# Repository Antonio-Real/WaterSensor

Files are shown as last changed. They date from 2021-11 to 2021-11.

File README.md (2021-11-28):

# **WaterSensor project**
 Wireless sensor for monitoring the level of a remote water tank.

 The motivation for this small home project came from the need to monitor the water level of a water tank used for watering. When the tank empties it causes air to fill the pipes and hoses, making it a bit of a pain to get out. With this system its easier to know when the tank is about to empty and flip a switch to turn on a water pump (in the future this system will automatically control the pump).

 ## **System overview**

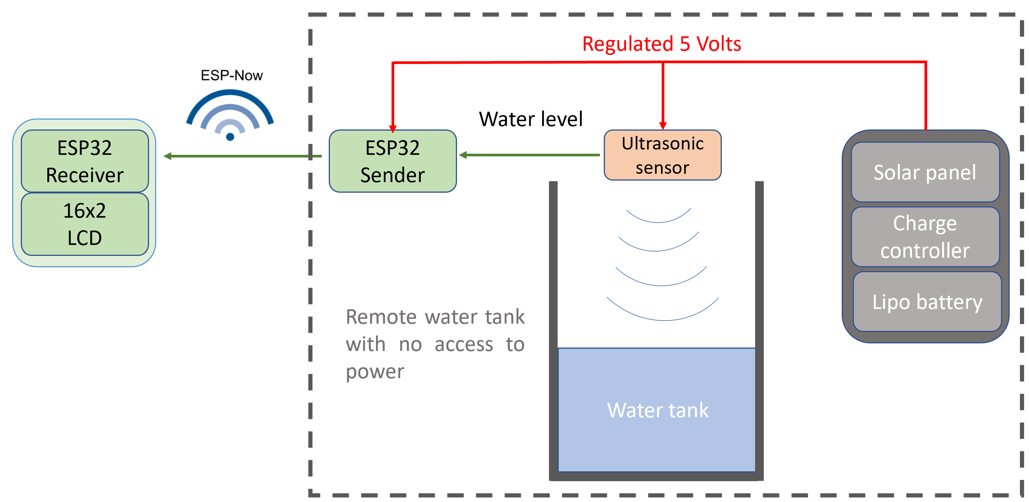
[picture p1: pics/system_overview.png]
system_overview
 

In simple terms, the water level is read by a HC-SR04 ultrasonic sensor which works well on water and doesn't corrode like those contact sensors you dip into water. The sensor data is acquired by a ESP32 and sent to a second ESP32 in another location using ESP-NOW which works well over longer distances and has smaller overhead than WIFI. The water level is then displayed on a standard 16x02 LCD.

One of the challenges of the system came from the fact that the water tank is in a place with no power, so a solar panel made sense to power the sensor and microcontroller. A charge controller and a Lipo battery work together with the solar panel to regulate power to a stable 5V and provide power in periods of no sun. The ESP32 sender board was custom designed to have minimal components to save battery.

## **Materials/tools used**

- 5W Solar panel and solar power management module bought from [Waveshare](https://www.waveshare.com/solar-power-manager.htm).
- 1800 mAh Lipo battery.
- Custom designed ESP32 board.
- HC-SR04 Ultrasonic sensor.
- A second generic ESP32 board + 16x02 LCD.
- Creality Ender 3v2 for printing the enclosures for the PCB, sensor and power module to protect from dust.

## **Repository contents**

| Folder/Files | Description |
| --- | --- |
| [pcb](/pcb) | Details and CAD files of the custom ESP32 board made for this project |
| [firmware](/firmware)  | Firmware of both the receiver and sender ESP32 boards |
| [models](/models) | STL files of the 3D printed parts for the enclosures |

## **Pictures**

parts_pic

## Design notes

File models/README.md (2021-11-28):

# **3D models in STL format**

Models that I fully designed in solidworks:
 - [Case](/models/custom_pcb_case) for custom PCB.

Models found in Thingiverse:
- [Clamp](/models/clamp) with gopro mounting system found [here](https://www.thingiverse.com/thing:4561329).
- [HC-SR04 case](/models/hcsr04_case) found [here](https://www.thingiverse.com/thing:3738687) but I adapted it with a gopro mount so it works with the clamp.
- [Solar charger case](/models/solar_charger_case) found [here](https://www.thingiverse.com/thing:4614783) with some changes to make it slightly larger to accomodate the battery.
- [LCD case](/models/lcd_case) found [here](https://www.thingiverse.com/thing:3839594).

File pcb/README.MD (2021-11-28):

# **Wireless sensor board**

This PCB design was kept to a minimum in order to optimize power consumption since it will function on a lipo battery. The main features:

- AP2112 3.3V low dropout (~50mV drop at 100mA) regulator to step down from the 5V that comes from the battery circuit.
- ESP32 microcontroller responsible for reading the HC-SR04 sensor and sending it through ESP-NOW protocol to a second ESP32.
- Screw terminals to easily connect the battery and the HC-SR04 ultrasonic sensor.

The PCB was designed using **Kicad 5.99** nightly build (soon to be released as Kicad 6).

 <br/><br/>

## **Schematic**
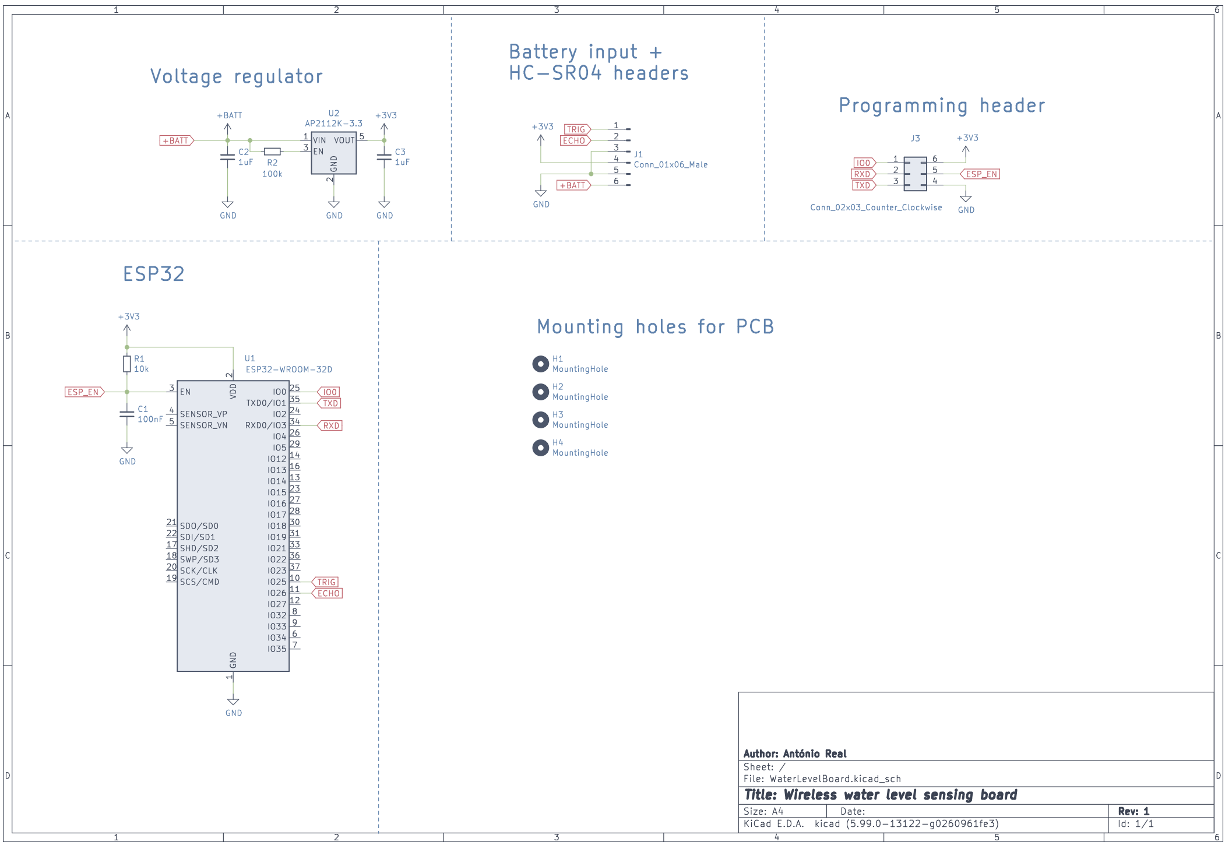
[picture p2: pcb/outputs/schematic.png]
pcb_sch


## **3D render of the PCB**
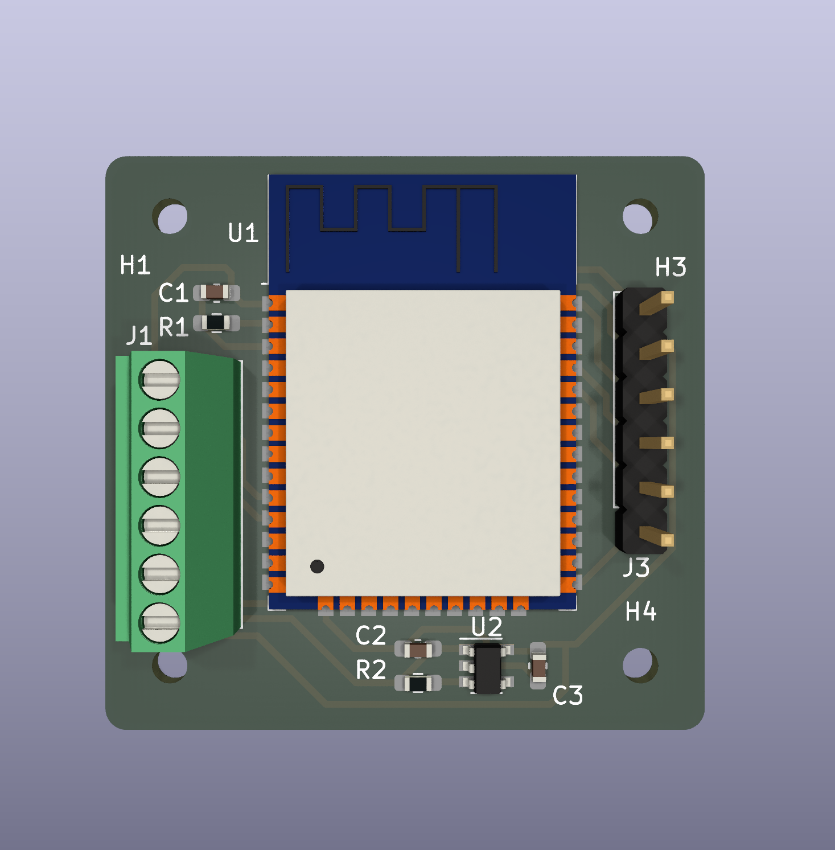
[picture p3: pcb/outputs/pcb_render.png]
pcb_render


## **Manufactured PCB**
The PCB was manufactured in a PCB milling machine and unfortunately came out poorly and required some enameled wire to replace the damaged tracks.
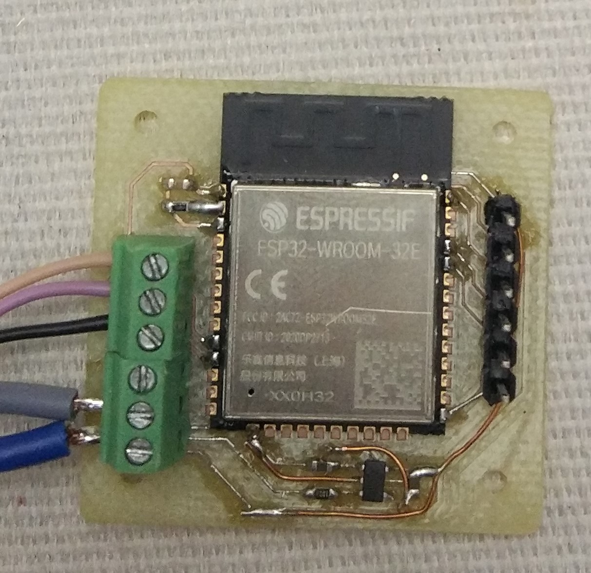
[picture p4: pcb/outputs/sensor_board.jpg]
pcb_manuf


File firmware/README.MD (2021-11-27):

# **Firmware of ESP32 water sensor sender/receiver**

The firmware was developed using VSCode with the PlatformIO extension and uses its build system and library management. Upon closer inspection of the `platformio.ini` file you can see two environments: `esp32_sender` and `esp32_receiver`. This was done to combine the firmwares of both boards in this repo since they're relatively simple.

By choosing one of the environments, the build system will automatically download the respective dependencies of each firmware and the respective main file (`main_sender.cpp` and `main_receiver.cpp`) found in `src` folder.

## **Common functionality**

In both boards Over-the-air (OTA) updates was included but we only want to run OTA when required. In a normal situation the boards will initialize ESP-NOW and communicate with each other but if GPIO 0 is pressed instead the boards initialize OTA and wait for the firmware to be uploaded.

## **Sensor sender**

This board is responsible for periodically taking a water level measurement with the HC-SR04 sensor and sending it to the receiver (receiver MAC address already known to the sender) using ESP-NOW  and then going back to sleep to maximize battery duration.

## **Sensor receiver**

This board is responsible for receiving the sensor readings and showing the values in percentage in a standard 16x02 LCD.

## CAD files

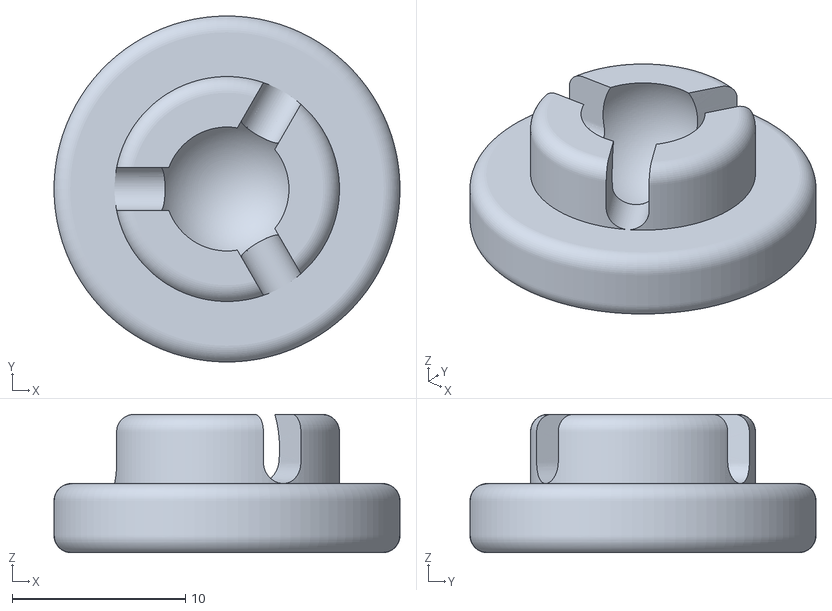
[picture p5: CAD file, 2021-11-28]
models/clamp/clamp_protector.stl
20.0 x 20.0 x 8.00

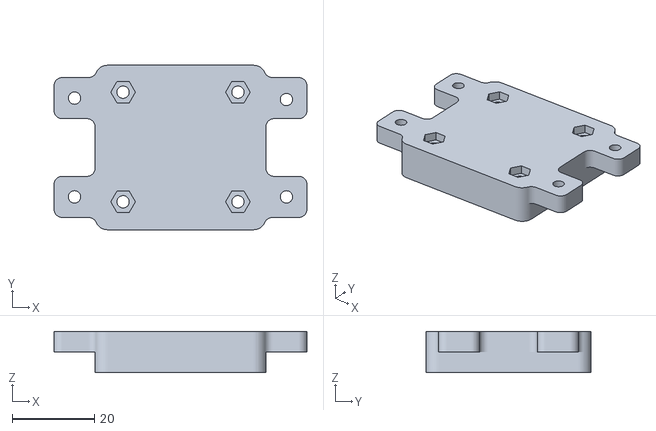
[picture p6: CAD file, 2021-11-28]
models/custom_pcb_case/pcb_case_bottom.STL
61.6 x 40.0 x 10.0

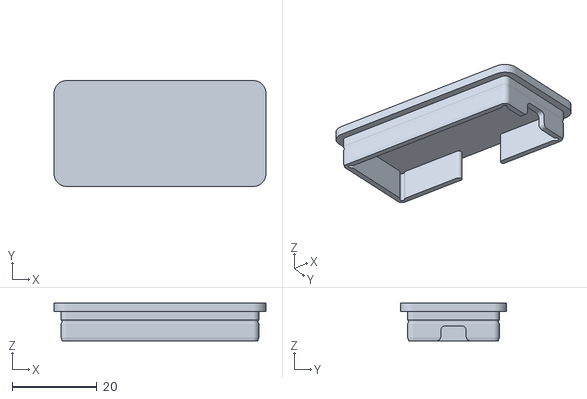
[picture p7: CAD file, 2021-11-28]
models/hcsr04_case/cover_hcsr04.STL
50.0 x 25.0 x 8.90

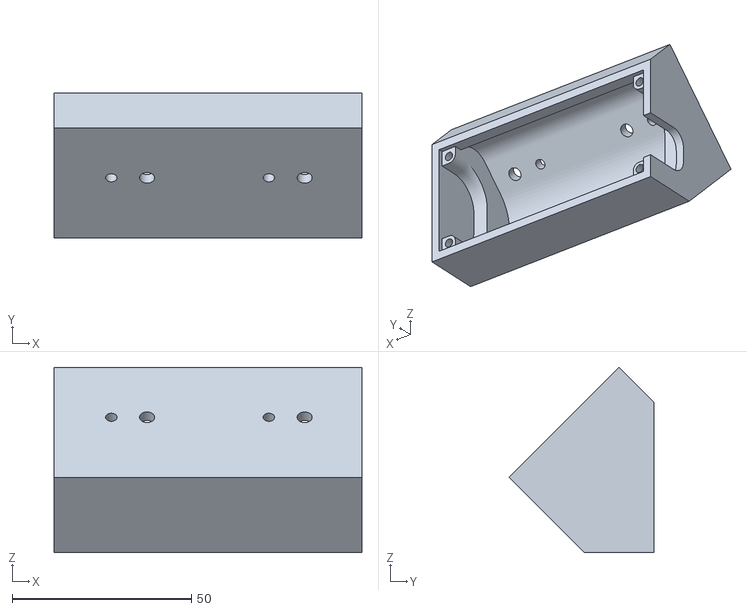
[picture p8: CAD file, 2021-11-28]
models/lcd_case/16x2_back_45deg_m3.stl
86.0 x 40.4 x 51.7

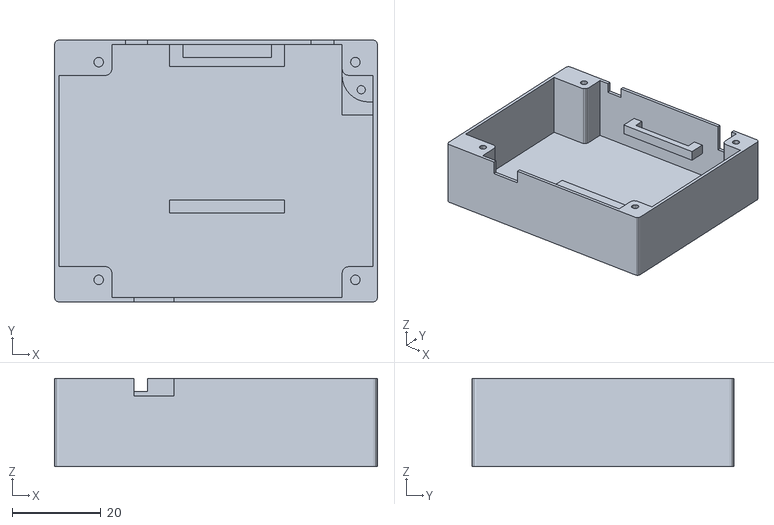
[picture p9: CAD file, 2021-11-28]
models/solar_charger_case/charger_case_top.STL
73.0 x 59.2 x 20.0

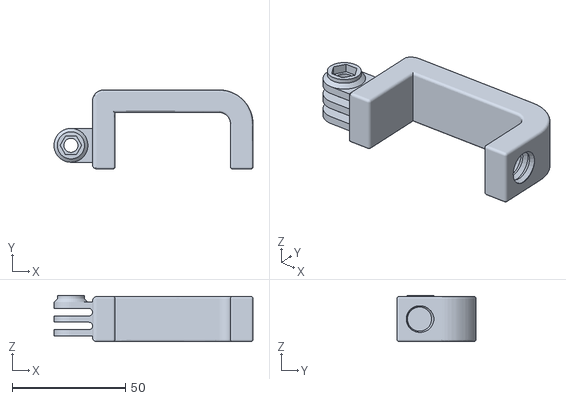
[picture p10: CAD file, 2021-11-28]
models/clamp/gopro_g-clamp.stl
88.0 x 35.0 x 20.5

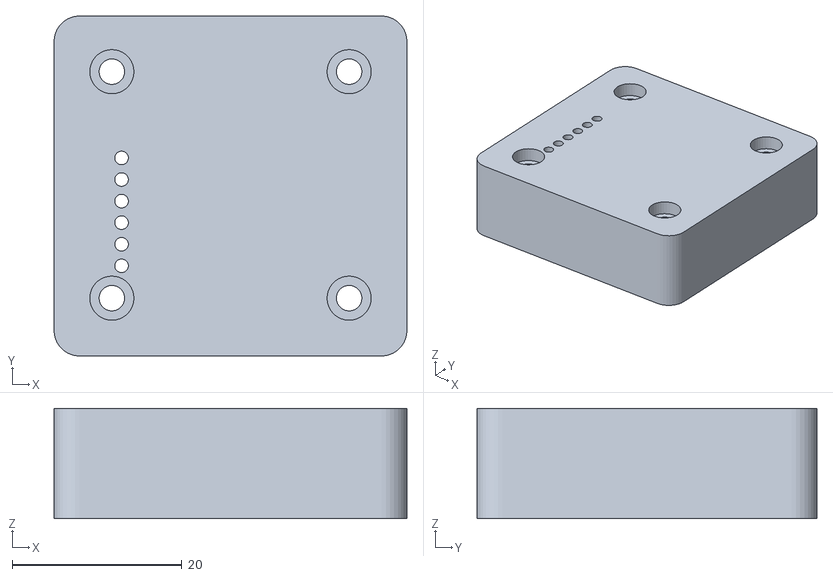
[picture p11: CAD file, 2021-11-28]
models/custom_pcb_case/pcb_case_top.STL
41.6 x 40.0 x 13.0

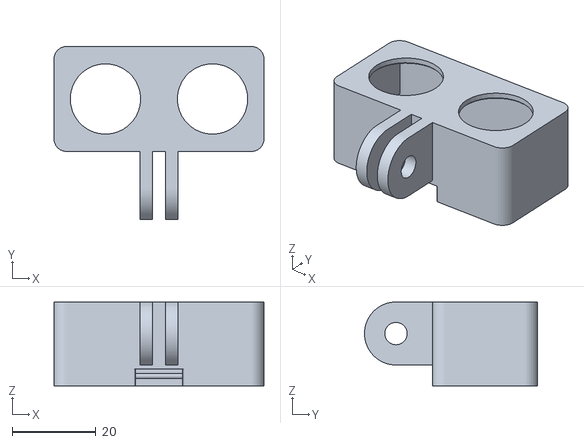
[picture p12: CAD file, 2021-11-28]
models/hcsr04_case/case_hcsr04.STL
50.0 x 41.2 x 20.0

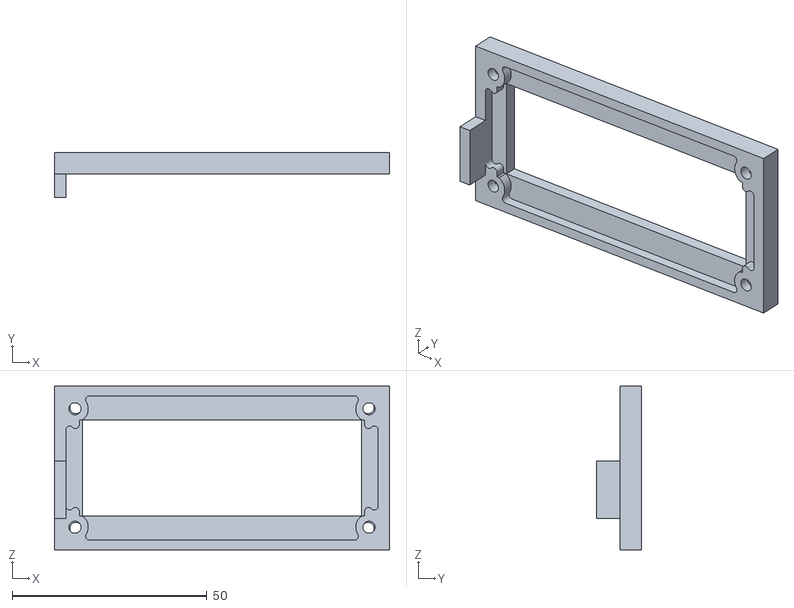
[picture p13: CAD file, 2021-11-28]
models/lcd_case/16x2_front_small_m3.stl
86.0 x 11.5 x 42.0

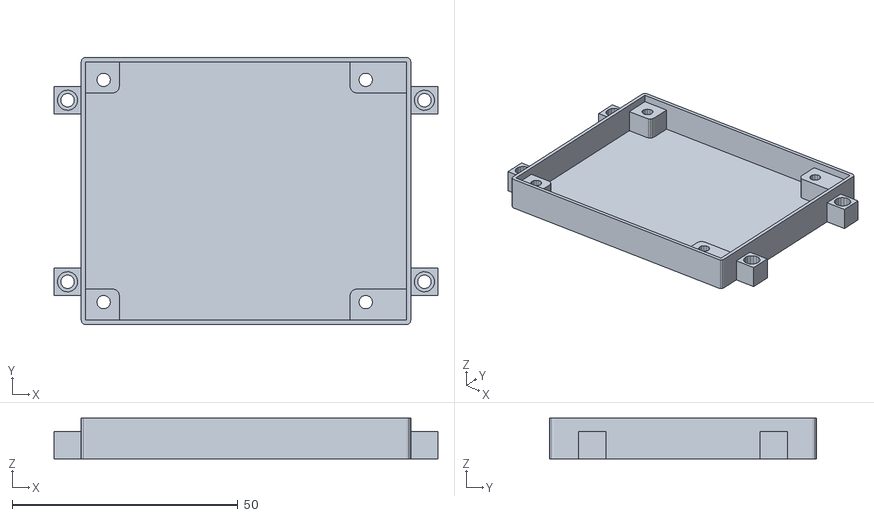
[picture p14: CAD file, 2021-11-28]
models/solar_charger_case/charger_case_bottom.STL
85.0 x 59.2 x 9.00

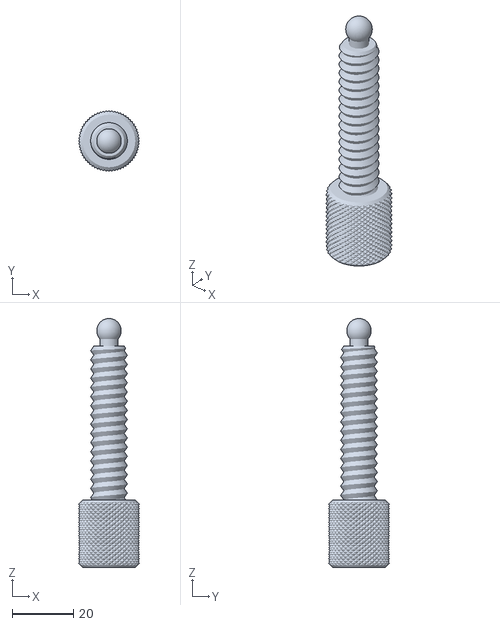
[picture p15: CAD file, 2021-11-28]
models/clamp/thread_and_knurling_knob_longHD.stl
19.8 x 19.8 x 81.3

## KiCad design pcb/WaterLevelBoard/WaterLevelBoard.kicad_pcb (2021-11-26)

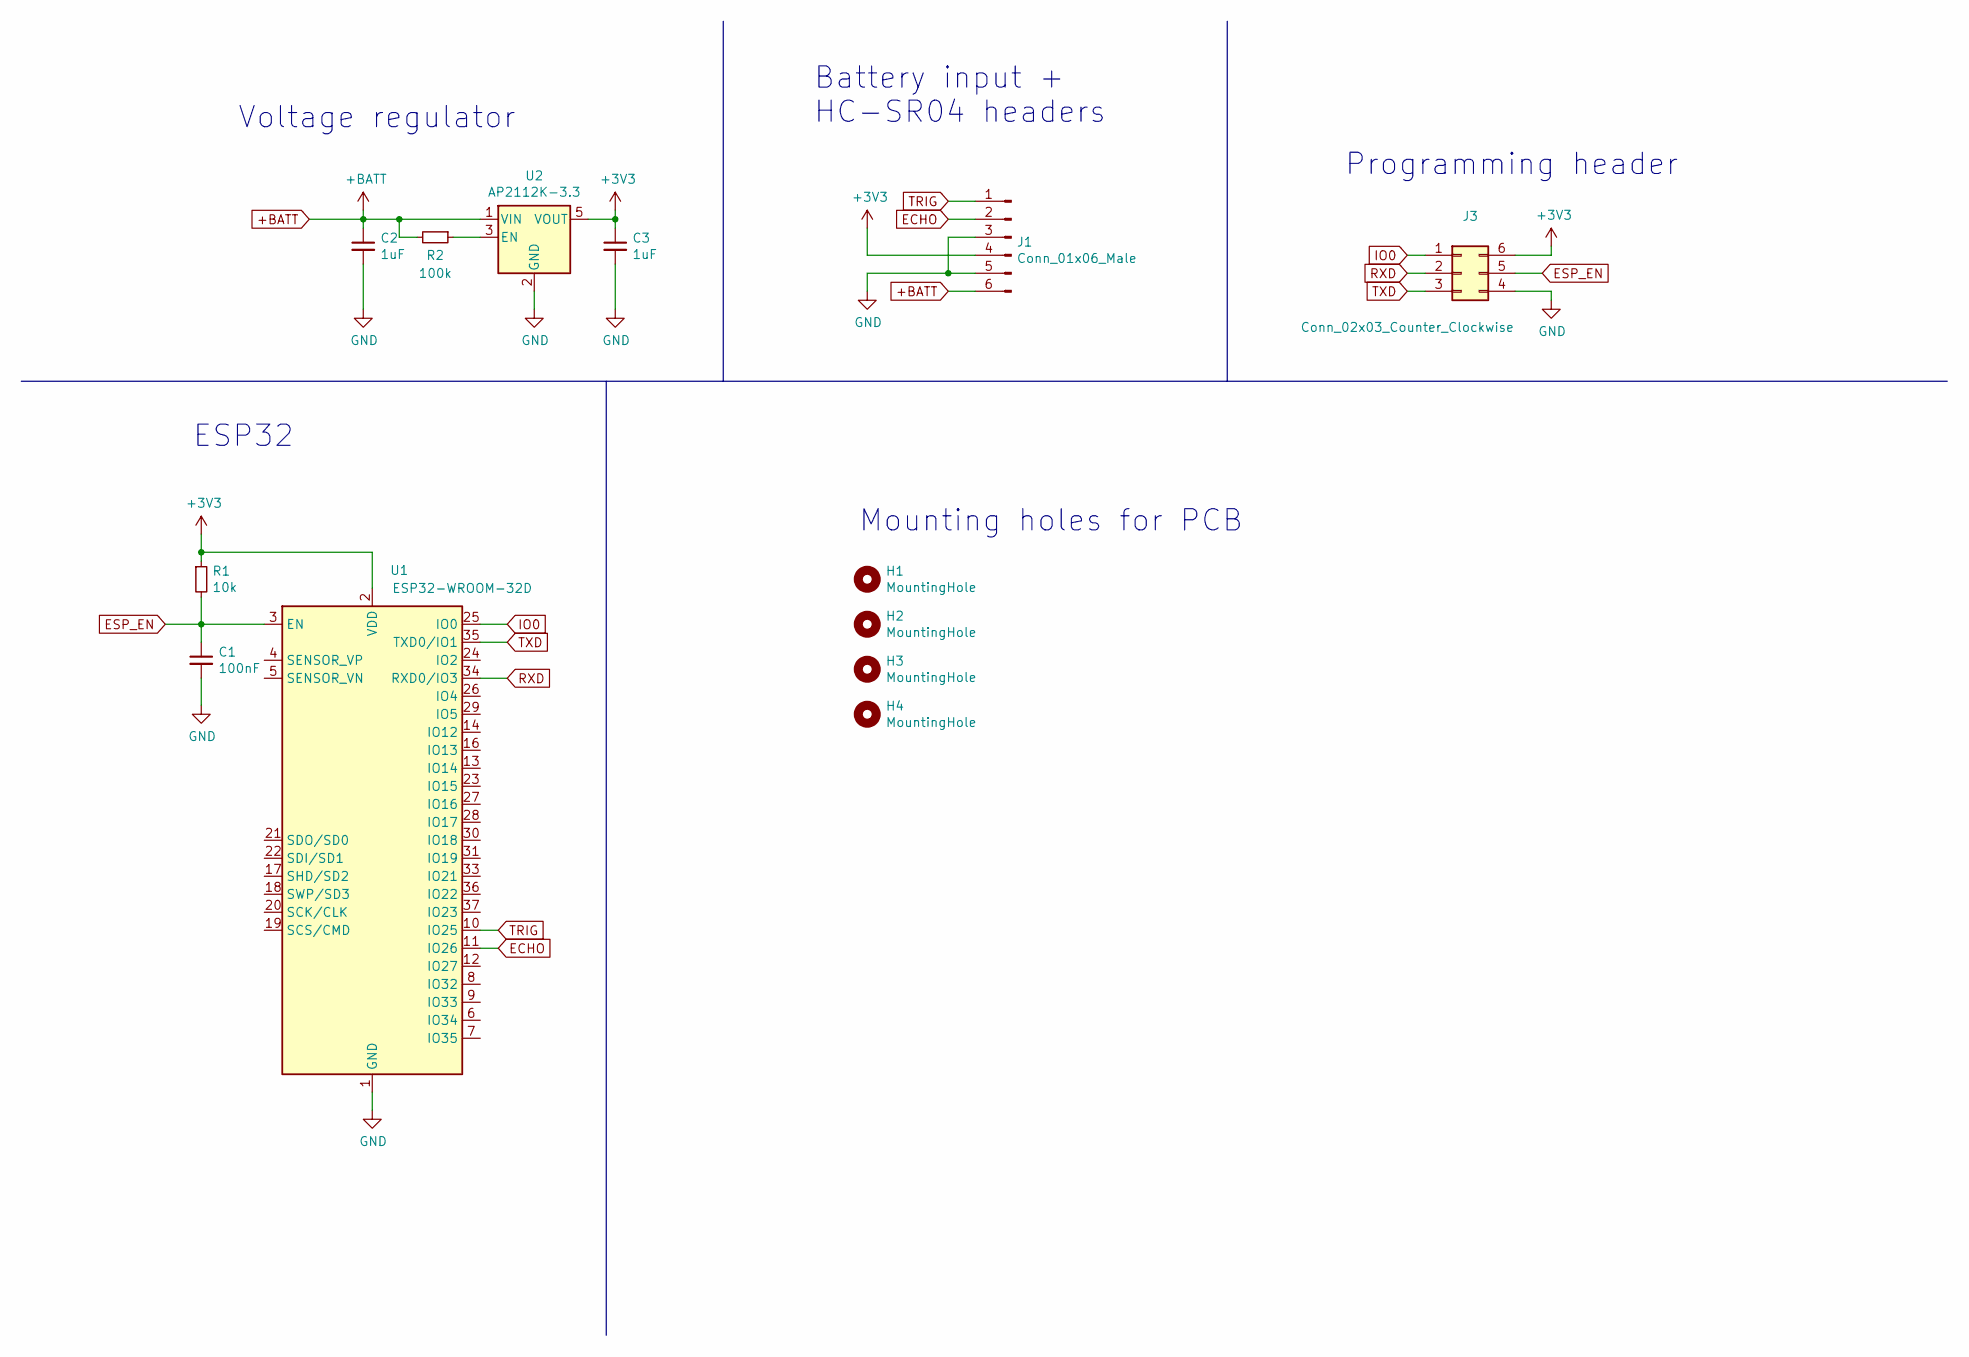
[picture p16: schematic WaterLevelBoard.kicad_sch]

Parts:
C1: 100nF; C_0603_1608Metric_Pad1.08x0.95mm_HandSolder
C2, C3: 1uF; C_0603_1608Metric_Pad1.08x0.95mm_HandSolder
H1, H2, H3, H4: MountingHole; MountingHole_2.1mm
J1: Conn_01x06_Male; TerminalBlock_Phoenix_MPT-0,5-6-2.54_1x06_P2.54mm_Horizontal
J3: Conn_02x03_Counter_Clockwise; PinHeader_1x06_P2.54mm_Vertical
R1: 10k; R_0603_1608Metric_Pad0.98x0.95mm_HandSolder
R2: 100k; R_0603_1608Metric_Pad0.98x0.95mm_HandSolder
U1: ESP32-WROOM-32D; ESP32-WROOM-32
U2: AP2112K-3.3; SOT-23-5

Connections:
+3V3: C3.1, J1.4, J3.6, R1.1, U1.2 (VDD), U2.5 (VOUT)
+BATT: C2.1, J1.6, R2.2, U2.1 (VIN)
ECHO: J1.2, U1.11 (IO26)
ESP_EN: C1.1, J3.5, R1.2, U1.3 (EN)
GND: C1.2, C2.2, C3.2, J1.3, J1.5, J3.4, U1.1 (GND), U1.15 (GND), U1.38 (GND), U1.39 (GND), U2.2 (GND)
IO0: J3.1, U1.25 (IO0)
unnamed: R2.1, U2.3 (EN)
RXD: J3.2, U1.34 (RXD0/IO3)
TRIG: J1.1, U1.10 (IO25)
TXD: J3.3, U1.35 (TXD0/IO1)

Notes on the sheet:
ESP32
Battery input + HC-SR04 headers
Mounting holes for PCB
Voltage regulator
Programming header

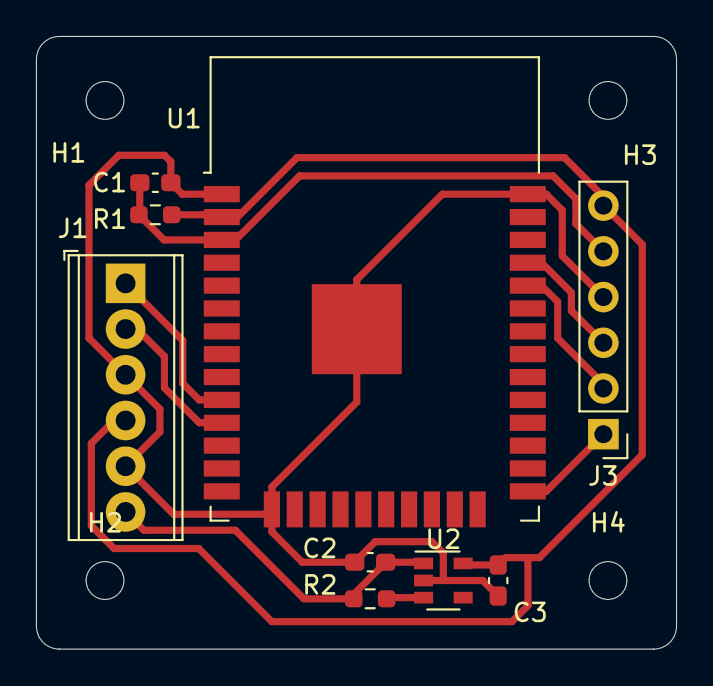
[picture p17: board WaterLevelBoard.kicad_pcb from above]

Board: 2 copper layers, 35.6 x 34.0 mm, 13 parts (0 on the bottom side), 10 nets.

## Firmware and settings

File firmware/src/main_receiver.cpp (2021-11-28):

#include <Arduino.h>
#include <ArduinoOTA.h>
#include <esp_now.h>
#include <WiFi.h>
#include <Wire.h>
#include <LiquidCrystal.h>

/**
 * @brief Constants and globals
 */
LiquidCrystal lcd(16, 5, 4, 2, 14, 13);

// Structure example to receive data
// Must match the sender structure
struct sensor_data {
    float dist;
};

sensor_data myData;
bool newData = false;

bool _otaEnabled = false;
const uint8_t ota_pin = 0;

// We'll assume 1 meter for now
const uint8_t waterTankHeight = 100;

/**
 * @brief Helper function for printing a string to the LCD
 * 
 * @param str String to be printed
 * @param row Row where string is printed (0 or 1)
 */
void displayString(String str, uint8_t row = 0) {
    lcd.setCursor(0, row);
    lcd.print("                ");
    lcd.setCursor(0, row);
    lcd.print(str);
}


/**
 * @brief Initializes Over-the-air updates and waits for firmware
 */
void setupOTA()
{
    _otaEnabled = true;
    // Wifi
    WiFi.softAP("Sensor receiver");

    ArduinoOTA.setRebootOnSuccess(true);
    ArduinoOTA
        .onStart([]()
                 {
                     String type;
                     if (ArduinoOTA.getCommand() == U_FLASH)
                         type = "sketch";
                     else // U_SPIFFS
                         type = "filesystem";

                     // NOTE: if updating SPIFFS this would be the place to unmount SPIFFS using SPIFFS.end()
                     ESP_LOGD(TAG, "Start updating %s", type.c_str());
                 })
        .onEnd([]()
               { ESP_LOGD(TAG, "\nEnd"); })
        .onProgress([](unsigned int progress, unsigned int total)
                    { ESP_LOGD(TAG, "Progress: %u%%\r", (progress / (total / 100))); })
        .onError([](ota_error_t error)
                 {
                     ESP_LOGD(TAG, "Error[%u]: ", error);
                     if (error == OTA_AUTH_ERROR)
                         log_i("Auth Failed");
                     else if (error == OTA_BEGIN_ERROR)
                         log_i("Begin Failed");
                     else if (error == OTA_CONNECT_ERROR)
                         log_i("Connect Failed");
                     else if (error == OTA_RECEIVE_ERROR)
                         log_i("Receive Failed");
                     else if (error == OTA_END_ERROR)
                         log_i("End Failed");
                 });

    ArduinoOTA.begin();

    displayString("OTA INIT");
}

/**
 * @brief Called every time data is received through ESP-NOW
 * 
 * @param mac Address of device that sent data
 * @param incomingData The received data
 * @param len length of the received data in bytes
 */
void onDataRecv(const uint8_t * mac, const uint8_t *incomingData, int len) {
    memcpy(&myData, incomingData, sizeof(myData));
    newData = true;
}

/**
 * @brief Initializes ESP-NOW for receiving water level data
 */
void setupESPNOW()
{
    // If the OTA pin is clicked, restarts the ESP32 and initializes OTA instead of ESP-NOW
    pinMode(ota_pin, INPUT_PULLUP);

    WiFi.mode(WIFI_STA);

    // Init ESP-NOW
    esp_err_t res1 =  esp_now_init();

    // Once ESPNow is successfully Init, we will register for recv CB to
    // get recv packer info
    esp_err_t res2 = esp_now_register_recv_cb(onDataRecv);

    if((res1 == ESP_OK) && (res2 == ESP_OK))
        displayString("ESPNOW INIT");
    else
        displayString("ESPNOW ERR");
}

void setup()
{

    #ifdef CORE_DEBUG_LEVEL
    Serial.begin(115200);
    #endif

    lcd.begin(16,2);
    
    // Test LCD
    displayString("LCD INIT");
    delay(1000);

    // If button was pressed at startup, means we want to setup WIFI AP for OTA
    esp_reset_reason_t reason = esp_reset_reason();

    if (reason == ESP_RST_SW)
        setupOTA();
    else
        setupESPNOW();
}

void loop()
{
    if (_otaEnabled)
        ArduinoOTA.handle();    
    else {
        if (digitalRead(ota_pin) == LOW)
            ESP.restart();

        if(newData) {
            int percentage = (myData.dist / waterTankHeight) * 100;
            percentage = constrain(percentage, 0, 100);
            
            log_i("%.2f\n", myData.dist);
            displayString(String(int(myData.dist)));
            displayString(String(percentage) + "%", 1);

            newData = false;
        }
    }
}

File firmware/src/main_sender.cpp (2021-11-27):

#include <Arduino.h>
#include <ArduinoOTA.h>
#include <esp_now.h>
#include <HCSR04.h>


/**
 * @brief Constants and globals
 */
UltraSonicDistanceSensor _distSensor(25, 26);

// Structure example to send data
struct sensor_data {
    float dist;
};

// The receiver ESP32 MAC address
const uint8_t peerMacAddr[] = {0xB4, 0xE6, 0x2D, 0xB2, 0xA9, 0xD1};

bool _otaEnabled = false;
uint8_t ota_pin = 0;

/**
 * @brief Initializes Over-the-air updates and waits for firmware
 */
void setupOTA()
{
    _otaEnabled = true;
    
    // Wifi
    WiFi.softAP("Sensor sender");

    ArduinoOTA.setRebootOnSuccess(true);
    ArduinoOTA
        .onStart([]()
                 {
                     String type;
                     if (ArduinoOTA.getCommand() == U_FLASH)
                         type = "sketch";
                     else // U_SPIFFS
                         type = "filesystem";

                     // NOTE: if updating SPIFFS this would be the place to unmount SPIFFS using SPIFFS.end()
                     log_i("Start updating %s", type.c_str());
                 })
        .onEnd([]()
               { log_i("\nEnd"); })
        .onProgress([](unsigned int progress, unsigned int total)
                    { log_i("Progress: %u%%\r", (progress / (total / 100))); })
        .onError([](ota_error_t error)
                 {
                     log_i("Error[%u]: ", error);
                     if (error == OTA_AUTH_ERROR)
                         log_i("Auth Failed");
                     else if (error == OTA_BEGIN_ERROR)
                         log_i("Begin Failed");
                     else if (error == OTA_CONNECT_ERROR)
                         log_i("Connect Failed");
                     else if (error == OTA_RECEIVE_ERROR)
                         log_i("Receive Failed");
                     else if (error == OTA_END_ERROR)
                         log_i("End Failed");
                 });

    ArduinoOTA.begin();
}

/**
 * @brief Called every time data is sent through ESP-NOW
 * 
 * @param mac_addr the receiver MAC address
 * @param status the transaction status
 */
void onDataSent(const uint8_t *mac_addr, esp_now_send_status_t status)
{
    log_i("\r\nLast Packet Send Status:\t");
    log_i("%s\n", status == ESP_NOW_SEND_SUCCESS ? "Delivery Success" : "Delivery Fail");
}

/**
 * @brief Initializes ESP-NOW for sending water level data
 */
void setupESPNOW()
{
    pinMode(ota_pin, INPUT_PULLUP);

    // Set device as a Wi-Fi Station
    WiFi.mode(WIFI_STA);

    esp_err_t res = esp_now_init();

    log_i("%s\n", res == ESP_OK ? "ESP OK" : "ESP ERR");

    // Once ESPNow is successfully Init, we will register for Send CB to
    // get the status of Trasnmitted packet
    res = esp_now_register_send_cb(onDataSent);

    
    log_i("%s\n", res == ESP_OK ? "ESP OK" : "ESP ERR");
    // Register peer
    esp_now_peer_info_t peerInfo;
    memcpy(peerInfo.peer_addr, peerMacAddr, 6);
    peerInfo.channel = 0;
    peerInfo.encrypt = false;

    // Add peer
    res = esp_now_add_peer(&peerInfo);
    
    log_i("%s\n", res == ESP_OK ? "ESP OK" : "ESP ERR");
}

void setup()
{
    #ifdef CORE_DEBUG_LEVEL
    Serial.begin(115200);
    #endif
    // If button was pressed at startup, means we want to setup WIFI AP for OTA
    esp_reset_reason_t reason = esp_reset_reason();

    if (reason == ESP_RST_SW)
        setupOTA();
    else
        setupESPNOW();
}

void loop()
{
    if (_otaEnabled)
        ArduinoOTA.handle();

    else {
        if(digitalRead(ota_pin) == LOW)
            esp_restart();
    

        sensor_data data;
        data.dist = _distSensor.measureDistanceCm();

        esp_err_t res = esp_now_send(peerMacAddr, (uint8_t *) &data, sizeof(data));
        
        log_i("%s\n", res == ESP_OK ? "ESP OK" : "ESP ERR");
        log_i("%.2f\n", data.dist);
        
        delay(100);
    }
}

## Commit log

2021-11-27 Documented code and added README files to PCB and Firmware folders
2021-11-28 Added 3D models used and added READMES to all folders
    [16x2_back_45deg_m3.stl, 16x2_front_small_m3.stl, case_hcsr04.STL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]
